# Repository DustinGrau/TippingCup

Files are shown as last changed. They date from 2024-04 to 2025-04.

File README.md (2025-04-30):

# Tipping Cup

Prop design by Dustin Grau

Originally created for use in Matilda the Musical, this device can also be used as a "possessed item" which will randomly move on its own.

Live prop demonstration (https://www.youtube.com/watch?v=uhK4_9nSQPM)

## Operation

There are 2 primary modes for operation: wobbling and tipping. In the wobble mode, the servo will randomly move a short distance to make the prop tilt, return to normal, then wait a random time before repeating. In the tipping mode the servo will go through a full 180&deg; movement to cause the cup to tip over.

## Parts

* [SG90 9g Micro Servo](https://a.co/d/7Wwkuhb) - This is a good balance between size and torque needed
* [Arduino Nano](https://a.co/d/5m9NQ1E) - We need a controller which can take inputs and use PWM control
* [2.4GHz RC Remote](https://a.co/d/b6ze1Bv) - Any micro remote transmitter/receiver is viable for use
* [DC Buck Converter](https://a.co/d/8IMmLeA) - Needed to bring the 9V power source down to 5V
* [9V Battery Connector](https://a.co/d/fDPGKFS) - Easy connector to a standard 9V battery
* Plastic Cup - Ideally no more than 6" tall, designed around a 84mm/3.3" base

## Models

See the "stl" folder for the necessary brackets and components for housing the electronics. The main bracket is a 2-part design which can be screwed together using M3 screws. The servo foot can be attached with a small length of metal such as a bent paperclip.

## Assembly

From the remote controlled tank the only components you truly need are the transmitter (handheld remote) and the radio receiver (green PCB) from inside the tank.

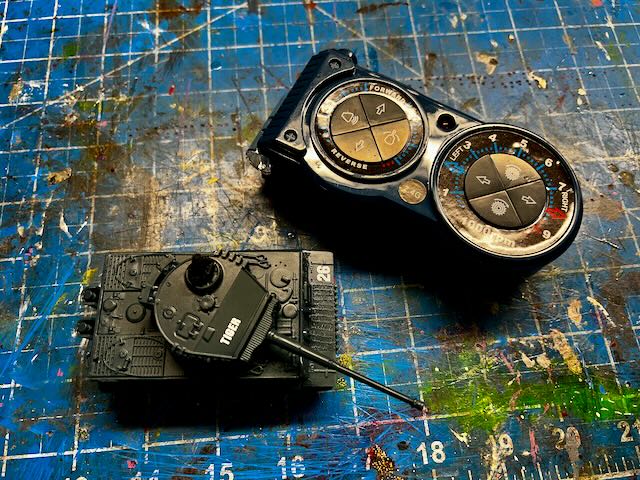
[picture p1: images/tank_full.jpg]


The motors, speaker, and battery connections will be cut away, leaving only the PCB. **Just be careful when cutting away the battery as you don't want to short the positive and negative wires together!**

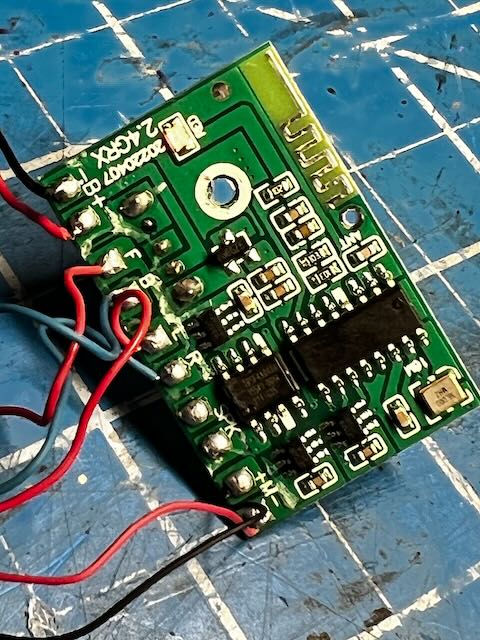
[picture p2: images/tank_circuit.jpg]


For power I used a 9V battery due to its availability and ability to provide enough current to the servo. This is connected to the buck converter which is set to 5V for output, which is what's expected by the Arduino and receiver. Note that it is a good idea to put a switch on the positive wire so you can easily turn off the device--leaving it on will cause the radio receiver to drain the battery.

`9V Battery --> Switch (positive) --> Buck Converter + (Input)`
`9V Battery --> Ground (negative) --> Buck Converter - (Input)`

The output of the buck converter is split to the Arduino and Servo motor to power both devices at the same time.

`Buck Converter (Output) --> Arduino Nano (VIN/GND) and Red/Brown on Servo`

For the Arduino Nano these are the pins used for power and the radio receiver:

- `VIN` to Buck output (+)
- `GND` to Buck output (-)
- `A1` to PCB `F`
- `A2` to PCB `B`
- `A3` to PCB `L`
- `A4` to PCB `R`
- `A5` to PCB `M+`
- `A6` to PCB `M-`
- `GND` to Receiver B (-)
- `3v3` to Receiver B (+)

For the Servo these are the connections needed to the Arduino Nano:

- Red (Power) to Buck output (+)
- Yellow (Data) to `D9` on Arduino Nano
- Brown (Ground) to Buck output (-)

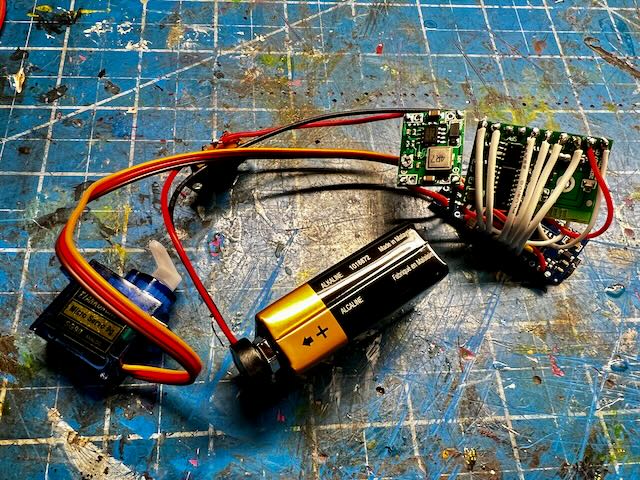
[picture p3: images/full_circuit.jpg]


Once the firmware is uploaded to the microcontroller, you will be able to control the servo using the remote control. The idea is that the servo will push on the "foot" to move the cup in the opposite direction. The software may need to be tuned depending on the size and weight of the cup used, adjusting the angle and range of motion.



Once placed within the printed housing, the device can reside inside the cup. Note that this was built around a specific plastic cup but the models can be altered as necessary if you have the skills. I use TinkerCAD for a lot of my projects which is free and easy to use.

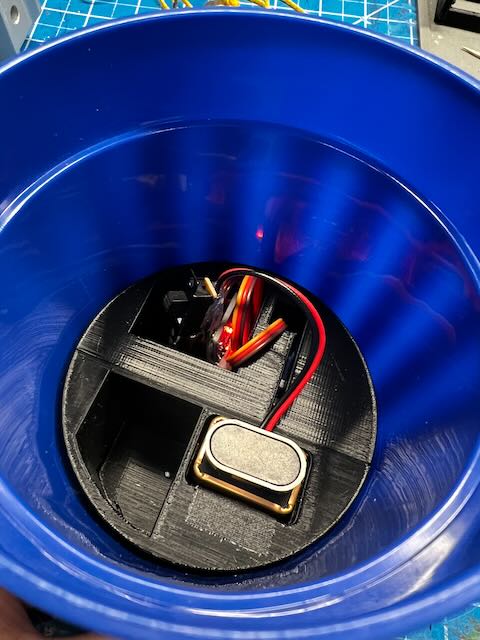
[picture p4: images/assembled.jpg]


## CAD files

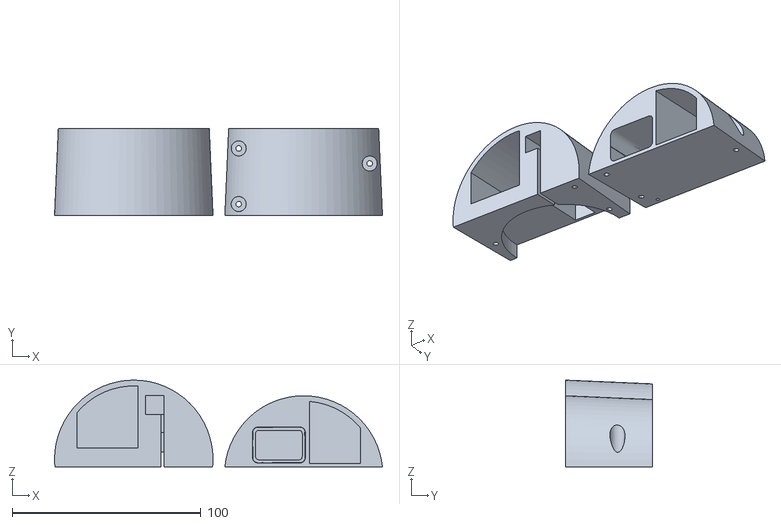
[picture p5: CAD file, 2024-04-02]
stl/Sliced Bracket.stl
173.8 x 46.0 x 46.0

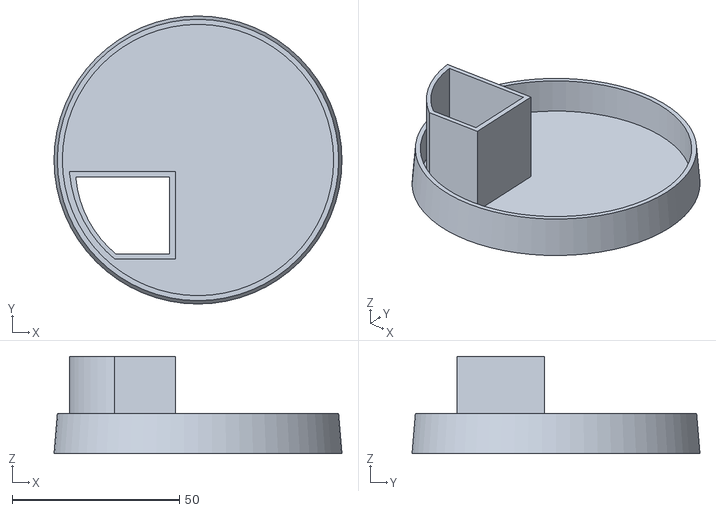
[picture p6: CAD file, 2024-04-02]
stl/Cup Top.stl
86.0 x 86.0 x 29.0

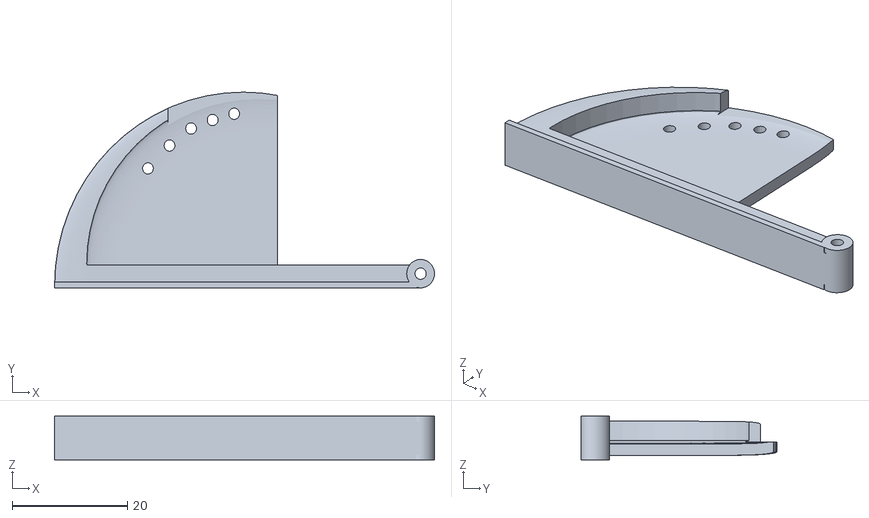
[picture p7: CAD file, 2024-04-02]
stl/Servo Foot.stl
66.0 x 34.0 x 7.60

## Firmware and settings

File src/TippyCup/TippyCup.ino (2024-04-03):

/**
 * Tipping Cup Prop
 * Detects voltage from specific pins on an Arduino Nano from an RC remote receiver.
 * Can operate in a "wobble" mode or fully "tip" when mounted inside a tall object.
 */

#include <Servo.h>

const int analogPinA1 = A1; // A1 pin, maps to the DOWN or RIGHT button on remote
const int analogPinA2 = A2; // A2 pin, maps to the UP or LEFT button on remote
const int analogPinA5 = A5; // A5 pin, maps to the TOGGLE button on remote
const int servoPin = 9;     // Digital pin for servo control (D9)
const int highThresh = 500; // Threshold for considering a pin as HIGH 
uint16_t servoPos = 0;      // Last-known servo position
boolean b_tipped = false;   // Indicates whether the servo was just in the "tipped" state.

Servo mainServo; // Create a servo object to control a servo motor

void setup() {
  Serial.begin(9600);

  pinMode(analogPinA1, INPUT);
  pinMode(analogPinA2, INPUT);
  pinMode(analogPinA5, INPUT);

  mainServo.attach(servoPin);
  delay(10);
  mainServo.write(0); // Reset to a known position
}

void loop() {
  // Read the analog values from the input pins.
  int sensorValueA1 = analogRead(analogPinA1);
  int sensorValueA2 = analogRead(analogPinA2);
  int sensorValueA5 = analogRead(analogPinA5);

  // Check if A5 is HIGH, meaning the device
  // should be doing a wobble action
  if (sensorValueA5 > highThresh) {
    // Move the servo some random angle, over some random period, every 10ms
    servoPos = moveServo(random(20, 45), random(200, 400), 10);
    delay(random(100, 300)); // Delay before next action

    // Add a very small movement at the peak of the last angle
    servoPos = moveServo(servoPos + 5, 300, 10);
    delay(random(200, 300)); // Delay before next action

    // Always reset to the default (upright) position, slowly
    servoPos = moveServo(0, 600, 10);
    delay(random(300, 500)); // Delay before next action
  } else {
    // Check if A1 is HIGH (reset)
    if (sensorValueA1 > highThresh) {
      if (resetPosition()) {
        delay(500); // Delay before next action
      }

      // Reset for next tipping event
      b_tipped = false;
    }

    // Check if A2 is HIGH (tip)
    if (sensorValueA2 > highThresh && !b_tipped) {
      // Immediately rotate the servo 180 degrees (tipped)
      servoPos = moveServo(180, 100, 10);
      delay(500); // Delay before next action

      // Return to a reset position
      if (resetPosition()) {
        delay(1000); // Delay before next action
      }

      // Set latch to ensure sensor state only
      // causes a single servo/tipping event
      b_tipped = true;
    }
  }
}

uint16_t moveServo(uint16_t i_servo_angle, uint16_t i_move_time, uint16_t i_step_time) {
  unsigned long startTime = millis(); // Get the current time

  while (millis() - startTime < i_move_time) {
    // Move the servo gradually to the target position
    int currentPos = map(millis(), startTime, startTime + i_move_time, servoPos, i_servo_angle);
    mainServo.write(currentPos);
    delay(i_step_time); // Adjust the delay to control the speed of the movement
  }

  mainServo.write(i_servo_angle); // Ensure the servo reaches the exact target position

  return i_servo_angle; // Return the new target position for the servo
}

boolean resetPosition() {
  boolean b_changed = false;

  // Immediately return the servo to 0 degrees (fully upright)
  if(mainServo.read() > 0) {
    mainServo.write(0); // Sets the desired position
    servoPos = mainServo.read(); // Confirm position
    b_changed = true; // Indicate change of position
  }

  return b_changed;
}
